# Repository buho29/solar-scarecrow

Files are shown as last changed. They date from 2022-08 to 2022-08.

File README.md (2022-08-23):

# Espantapájaros Solar

Para desanimar a los pájaros a usar nuestra huerta como un restaurante buffet-free
mi segundo intento de ahuyentar de forma not-letal (mi coche muchas veces vive en la calle)

### Descripción 

- "imita" el aleteo de un pájaro
- emite sonidos (mp3)
- solar (queda probar en dias nublados , en autonomia deberia dar para 4 dias sin luz)
- tiene un timón para que el búho gire según la dirección de el viento
- queda probar si es waterproof , uso una junta de un filamento de tpu de 1.75mm pegada con cyano, la electronica descansa sobre una esponja

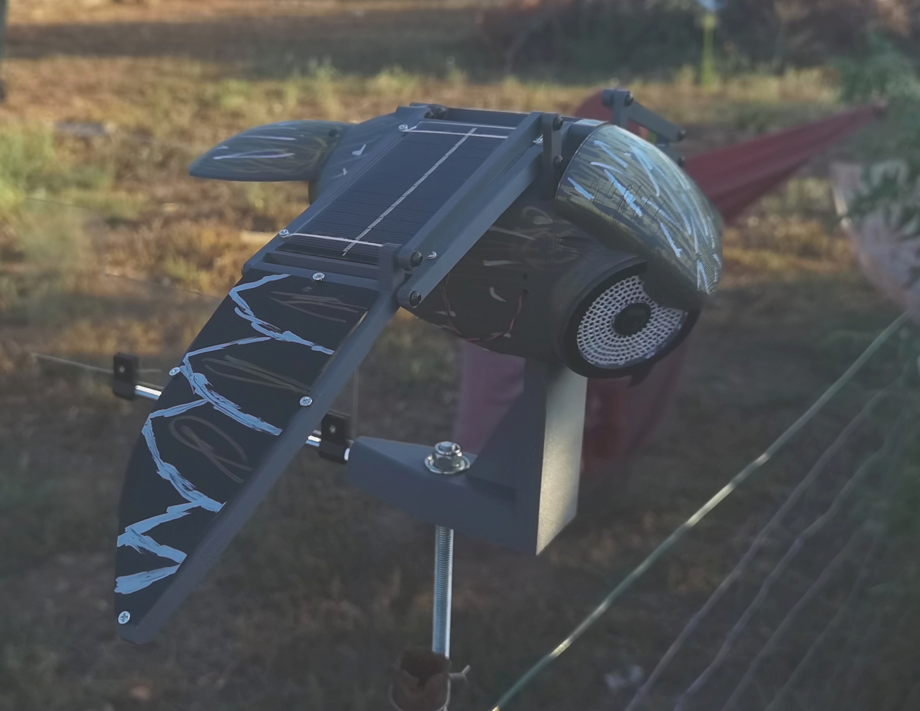
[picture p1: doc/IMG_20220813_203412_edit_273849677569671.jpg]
final


https://user-images.githubusercontent.com/47985666/186021702-38a5164b-d2b8-40fa-a175-db5c7b3ff85f.mp4

*Read this in other languages: [English](README.en.md)

# Ficheros 3D

https://user-images.githubusercontent.com/47985666/186019331-49d15a59-9388-4942-bd01-0e9cbd2d4d04.mp4

los ficheros para imprimir estan en [/stl](/stl).

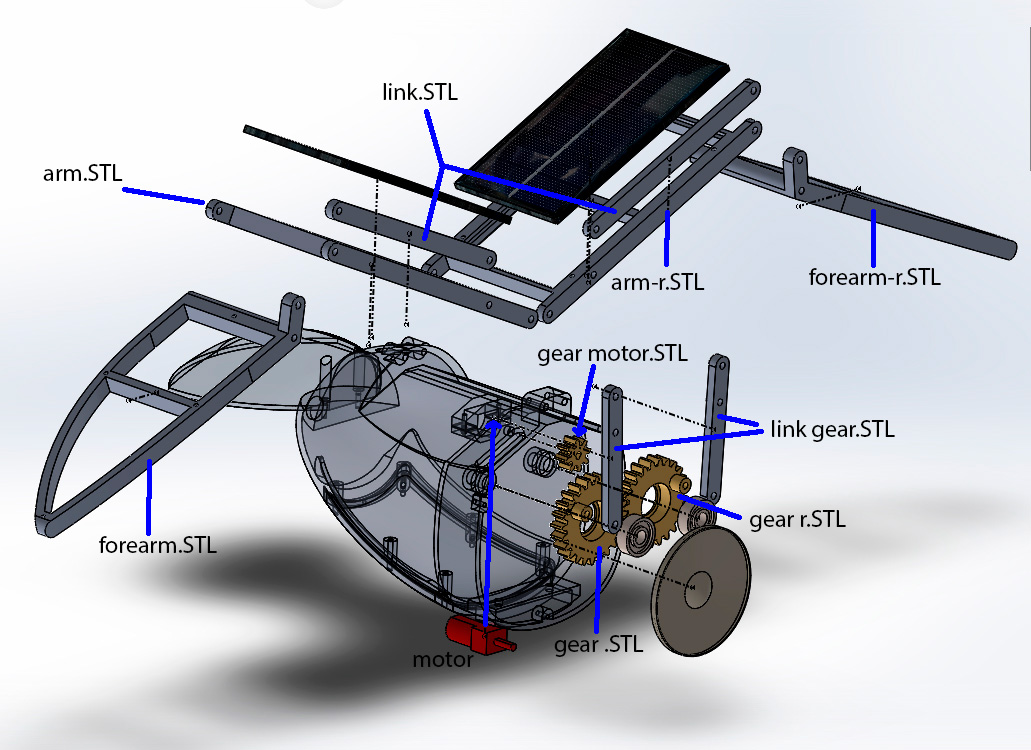
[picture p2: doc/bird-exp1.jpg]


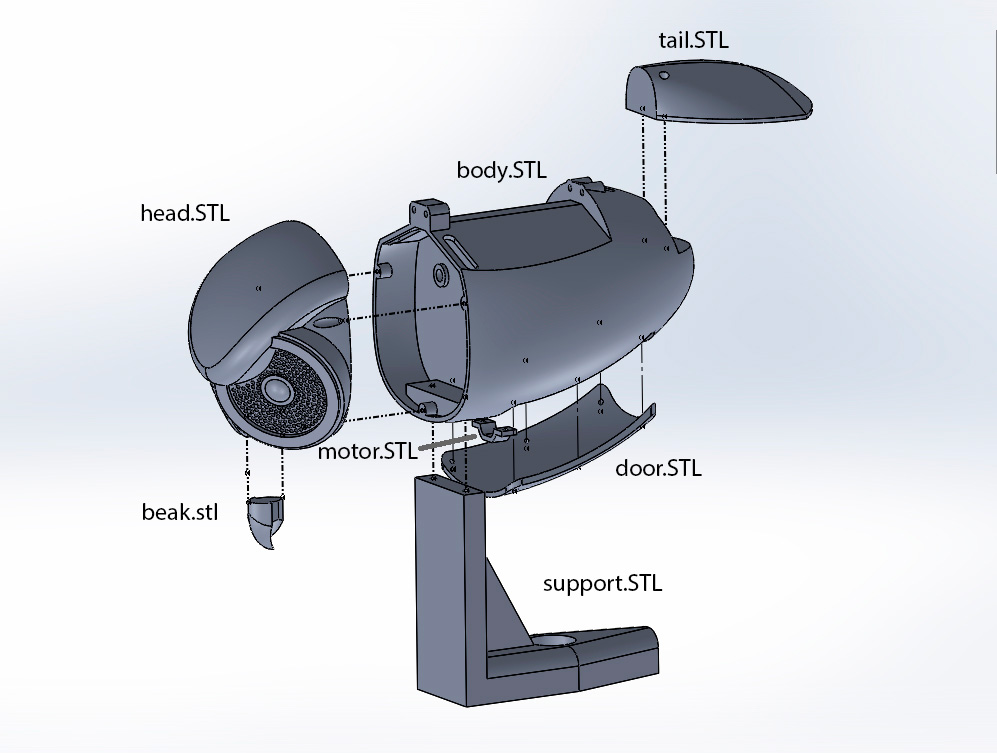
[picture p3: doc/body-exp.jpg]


> **Nota:** los ficheros fuentes de Solidworks 2018 3D estan [/solidworks](/solidworks).

# Hardware

Posiblemente no sea la mejor selección de los materiales pero es la que tenia...

## Suministro electrico

Uso un stepup para alimentar el esp32 y los motores con 6v, el stepup sube el voltaje 4.2v de las baterias a 6v

con el esp32 en modo sleep (ahoro) el consumo real es de 18ma (*24h)

Las 2 placas solares en paralelo bajo el sol me da unos 120ma/h 

Cargo las baterias con un tp4056 , 
necesitas baterías con protección de bajo voltaje , los bms habría sido mejor una mejor elección

Mido la corriente de las placas solares con una divisor de tension (7.2v -> 3.3v)

## Circuito 

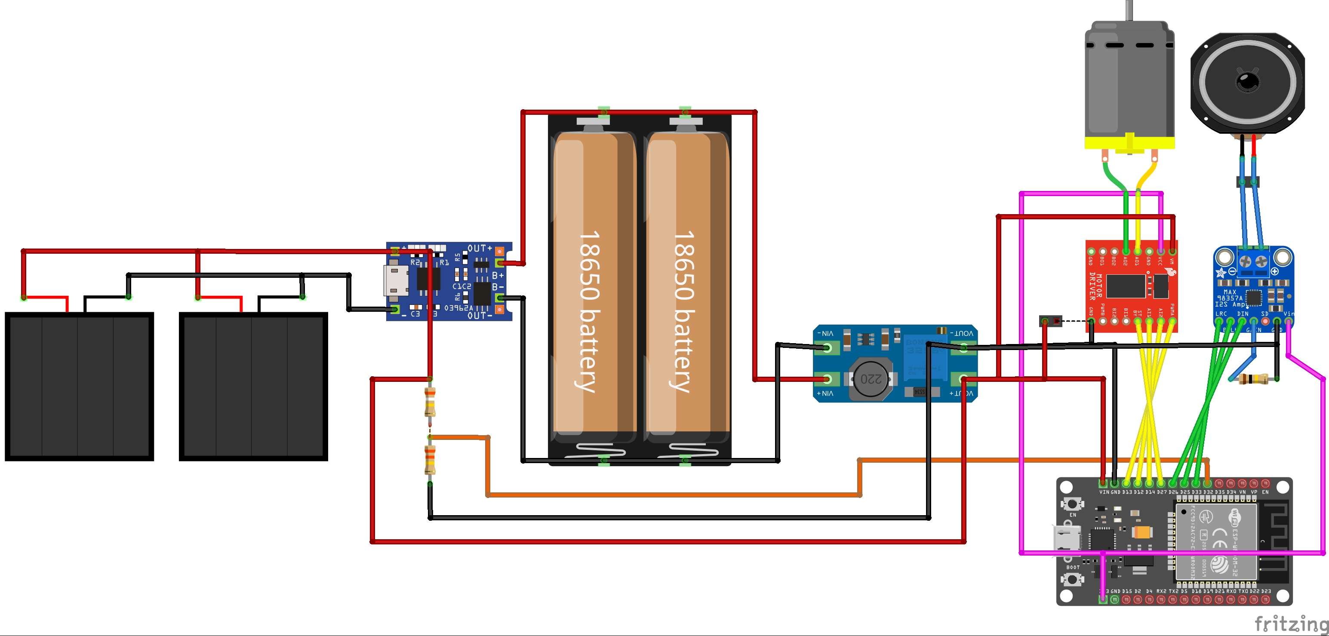
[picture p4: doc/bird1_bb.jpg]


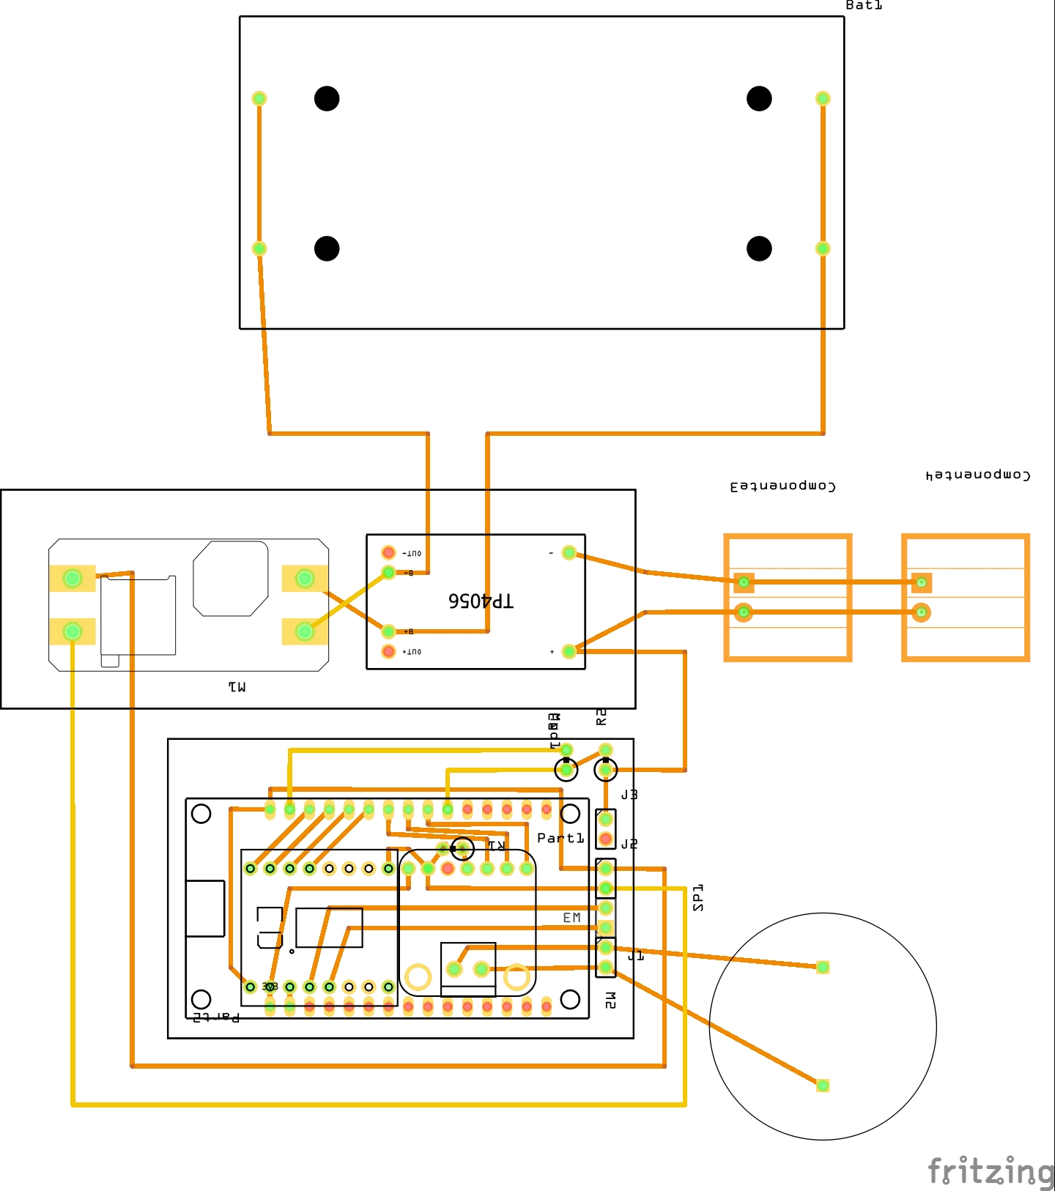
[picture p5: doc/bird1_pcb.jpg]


> **Nota:** los ficheros fuentes de fritzing estan [/electro](/electro).

## Arduino

- Hay que subir el directorio /Data al Spiff del esp32, contiene los *.mp3, se puede poner lo que quieras hasta 1.5mb (reggaton???)
https://github.com/me-no-dev/arduino-esp32fs-plugin

- Hay que instalar esta librería para el max
https://github.com/earlephilhower/ESP8266Audio

### Funcionamiento

```mermaid
flowchart  TD  
 A[Inicio]  -->  B{Es de dia?}  
 B  -- No --> C[Duerme 10min]  
 B  -- Si --> E{El contador es <br> un numero Par?}
 E -- Si --> F[10seg audio+motor]
 E -- No --> G[10seg solo motor]
 F --> C
 G --> C
 C --> B
```
### Variables

```c++
// config
// cuando acabe lo mandamos al modo sleep (ahoro de bateria) 10min 
const int timeSleep = 60 * 10  * uS_TO_S_FACTOR;
// el tiempo que funciona audio y el motor (10seg) 
const int timeRunning = 10 * 1000; 
// el volumen de el audio (maximo 3.99)
const float volume = 1.5;
//si el voltage es menor lo mandamos al sleep (se supone que es de noche)
const float minVoltage = 0.5; 
int _speed = 255; // velocidad del motor (0-255)

```

## Lista de la compra

> **Nota:** no tengo nada que ver con los vendedores, son los enlaces de mi compra.

1 x DC 6V N20 Mini Micro Metal Gear Motor with Gearwheel DC Motors 30 RPM
https://www.aliexpress.com/item/33022320164.html

1 x Dual Motor Driver 1A TB6612FNG
https://www.aliexpress.com/item/32223093678.html

3 x 3PIN and 1 x 2Pin PCB Screw Terminals Blocks Connector 2.54MM Pitch 
https://www.aliexpress.com/item/1005001711075410.html

2 x Mini 6V 1W Solar Panel 
https://www.aliexpress.com/item/32817603341.html

1 x Single Cell Micro USB Power Supply Board TP4056
https://www.aliexpress.com/item/32964995078.html

1 x MT3608 DC-DC Step Up Power
https://www.aliexpress.com/item/32671989238.html

1 x speaker waterproof 8 ohm 3W Diameter 57MM
https://www.aliexpress.com/item/1005002657272394.html

1 x 18650 Battery box double holder
https://www.aliexpress.com/item/4000098297232.html

1 x Max98357 I2S 3W Class D Amplifier
https://www.aliexpress.com/item/4000086613283.html

1 x Esp32 DEVKIT V1
https://a.aliexpress.com/_vYtC43

2x Battery 18650 with protection

### Otros

#### Rodamientos
2x 606ZZ 6x17x6mm (gears)
https://www.aliexpress.com/item/1005001826957482.html

2 x 608ZZ 8x22x7mm (rudder)
https://www.aliexpress.com/item/4001058241232.html

#### Tornilleria
wooden Self-tapping screw M2x8mm and M2x6mm
https://www.aliexpress.com/item/1005002336941795.html

18 x Screw M3 x 12mm
https://www.banggood.com/M3-Bolts-Stainless-Steel-Screws-Button-Head-Socket-Cap-10-Size-p-952124.html

### Herramientas
#### Brocas :
- 3mm(better 3.1) 
- 2.8mm (thread) 
- 2mm
- 1.6mm (thread)

## Galeria

gallery
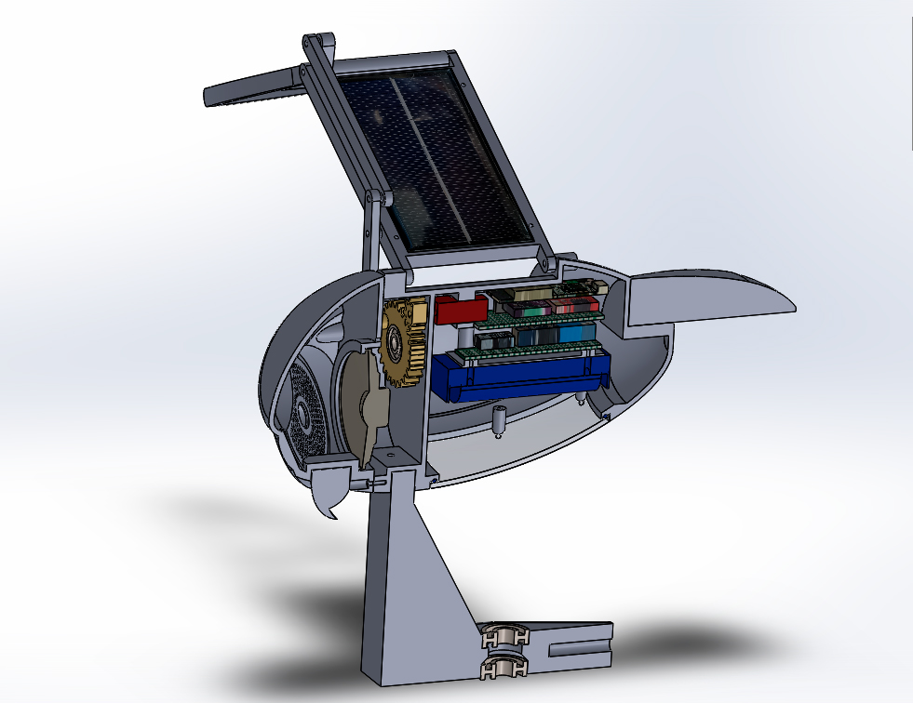
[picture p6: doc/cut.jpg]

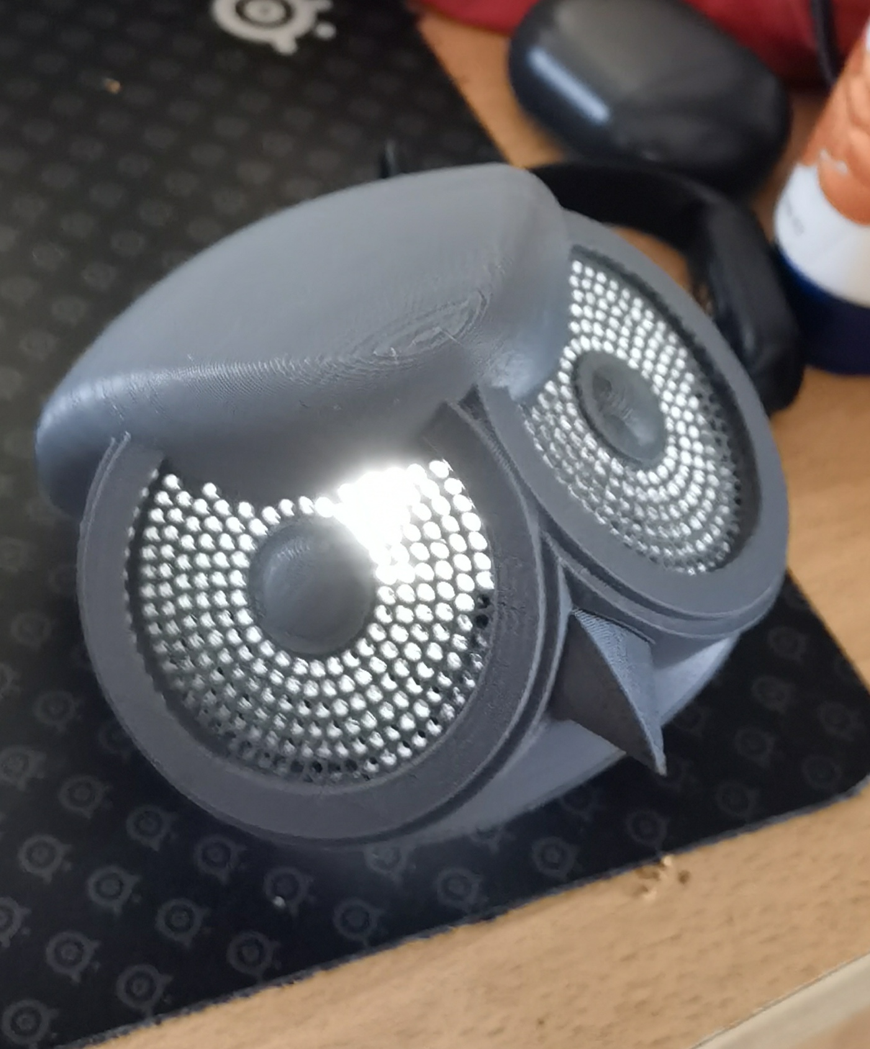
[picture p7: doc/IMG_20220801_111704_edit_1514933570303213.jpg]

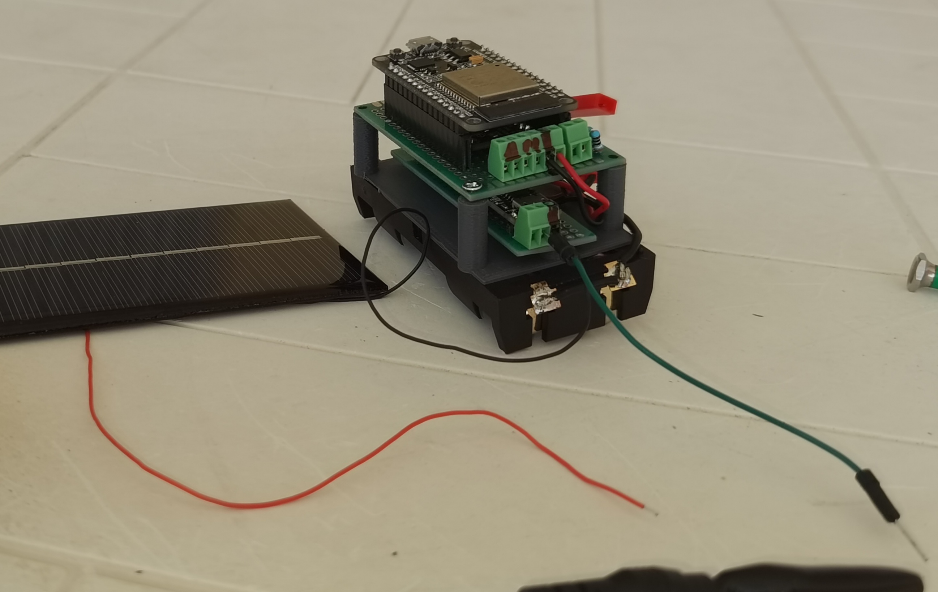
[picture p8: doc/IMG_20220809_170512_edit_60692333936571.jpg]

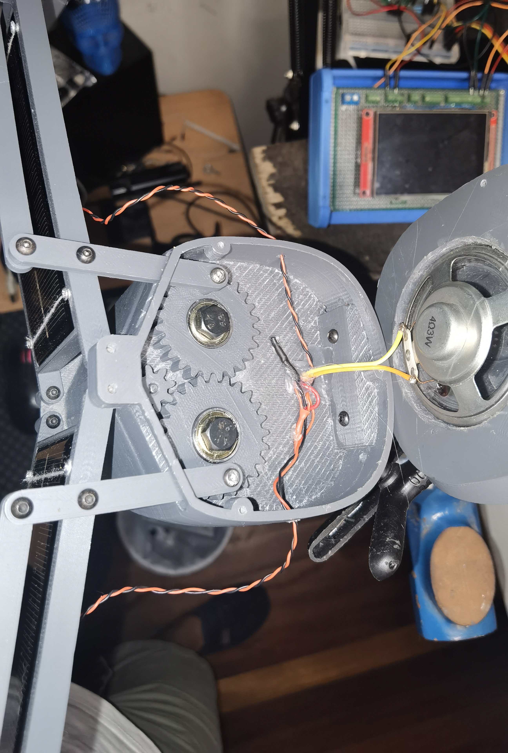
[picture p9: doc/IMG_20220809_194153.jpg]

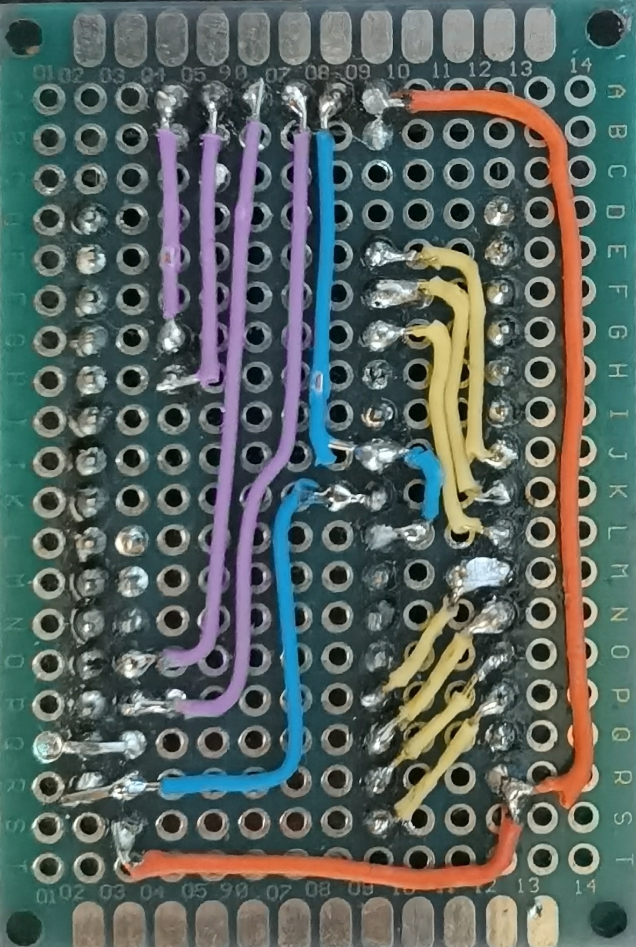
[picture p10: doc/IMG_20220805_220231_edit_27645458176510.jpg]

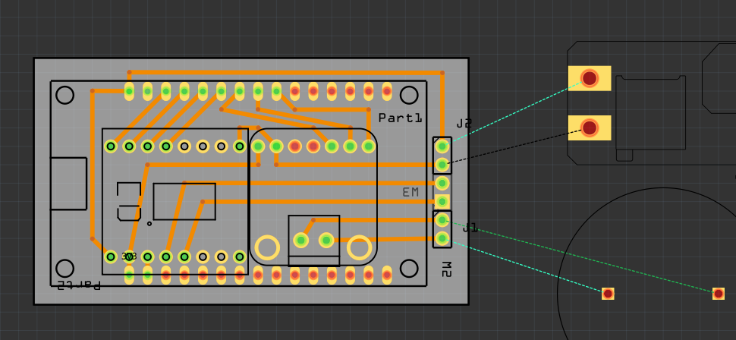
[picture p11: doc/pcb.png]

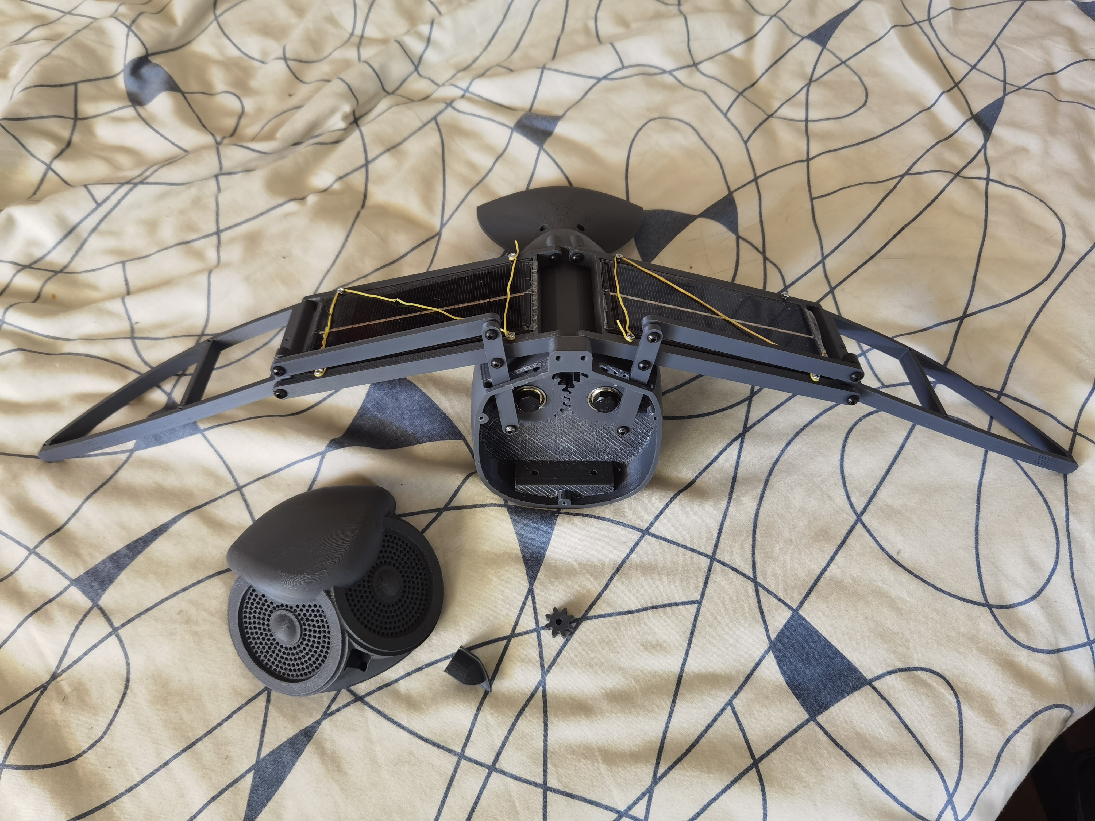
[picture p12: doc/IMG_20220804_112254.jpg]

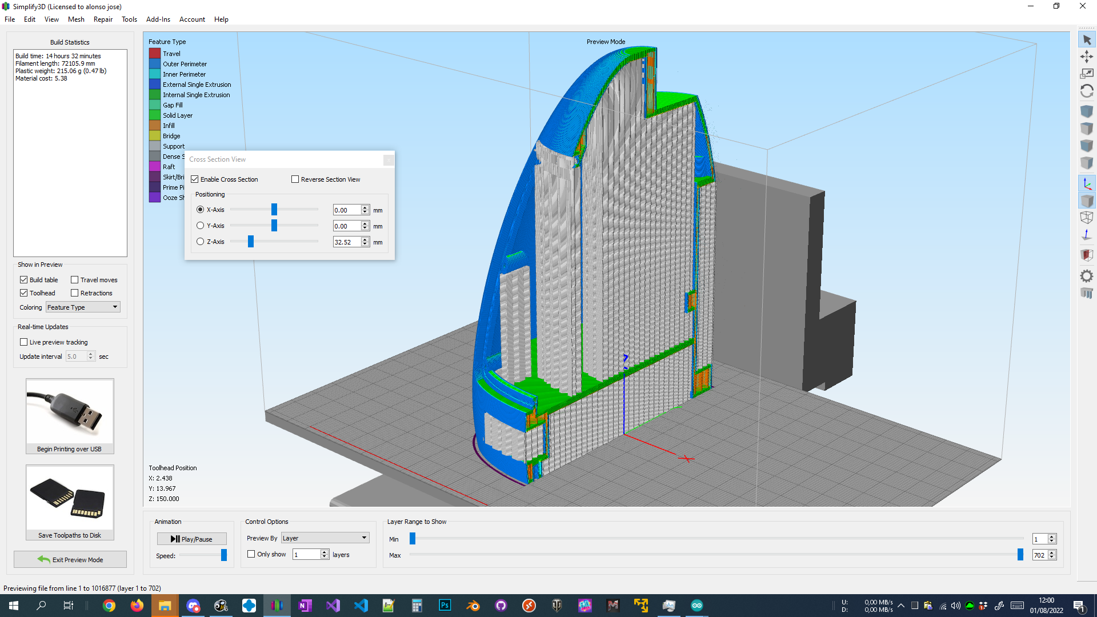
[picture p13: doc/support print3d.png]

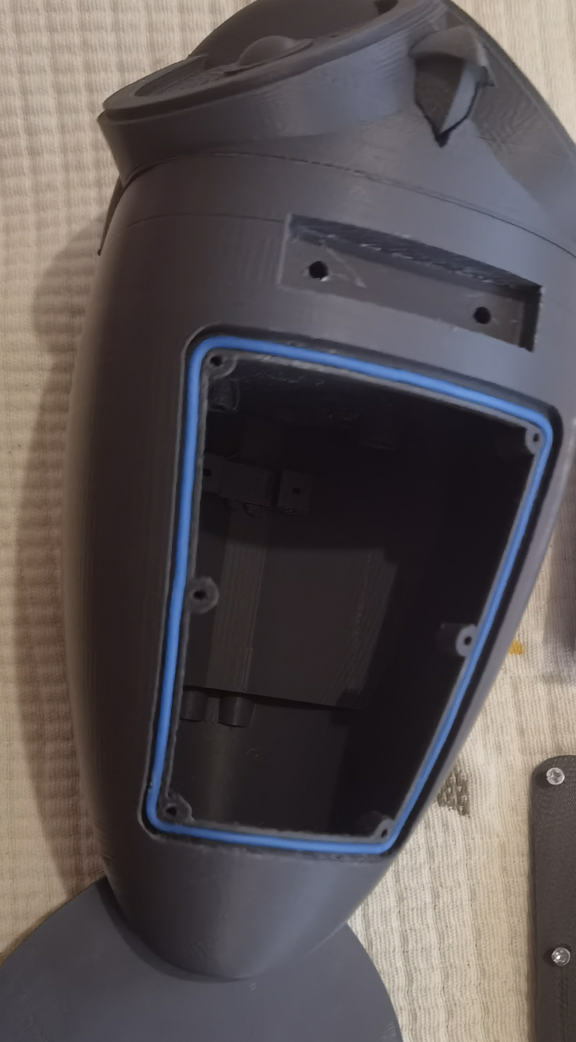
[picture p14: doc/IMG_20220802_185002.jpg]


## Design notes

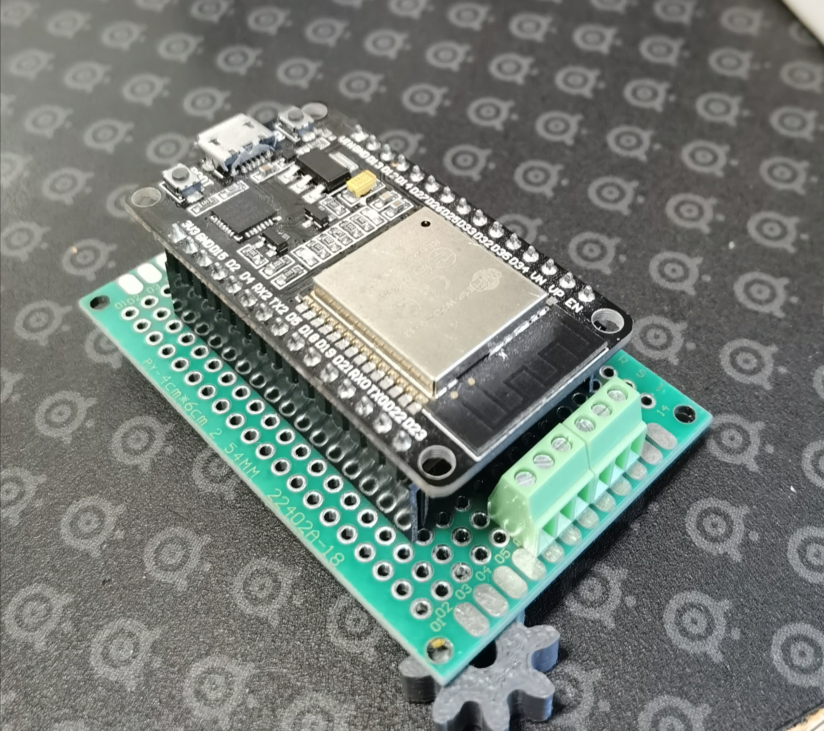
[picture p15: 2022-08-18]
doc/IMG_20220805_130451_edit_7011887212471.jpg

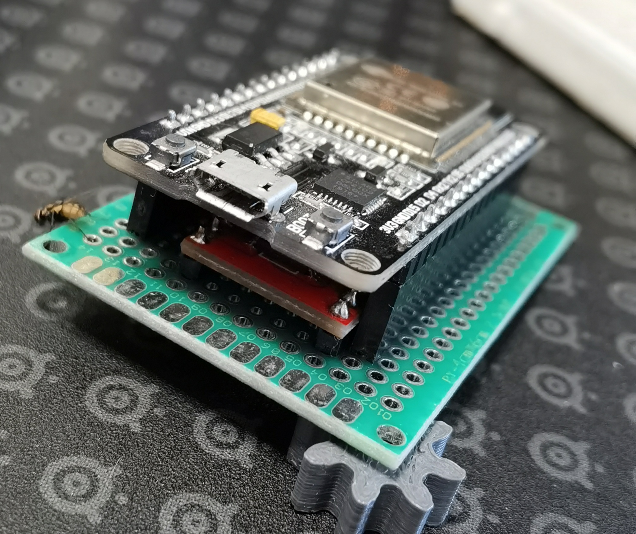
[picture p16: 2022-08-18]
doc/IMG_20220805_130421_edit_7032362407259.jpg

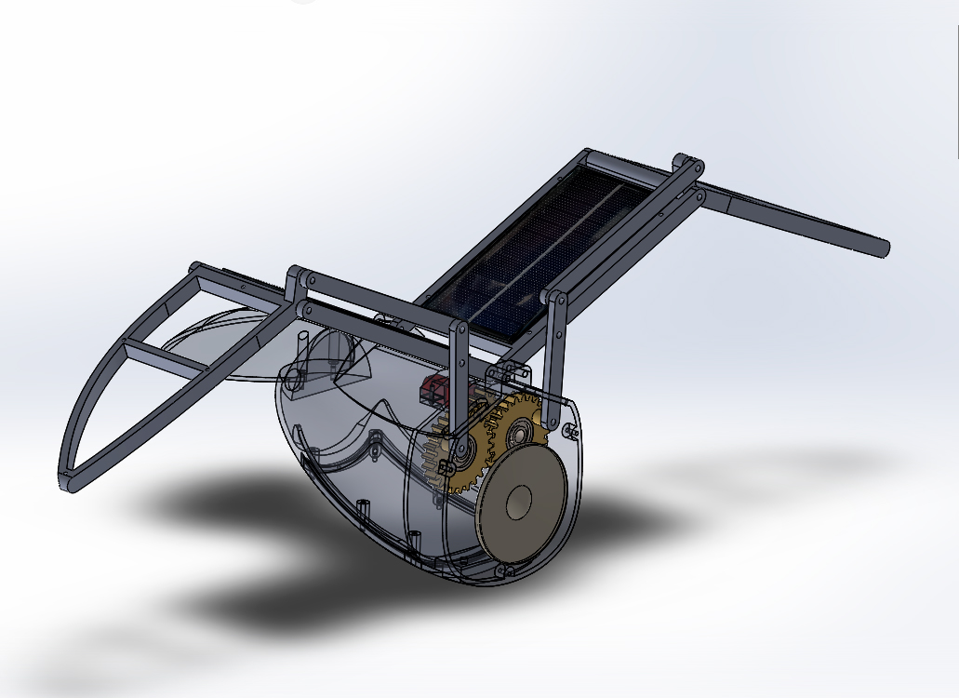
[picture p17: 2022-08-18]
doc/bird-exp.jpg

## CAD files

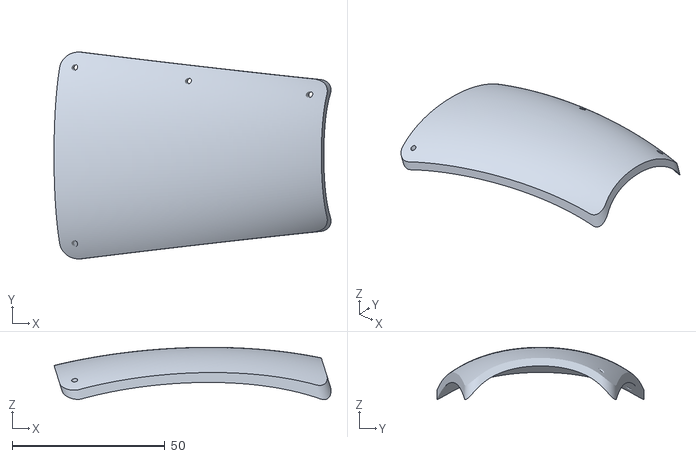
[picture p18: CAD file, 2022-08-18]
stl/door.STL
90.8 x 67.8 x 17.2

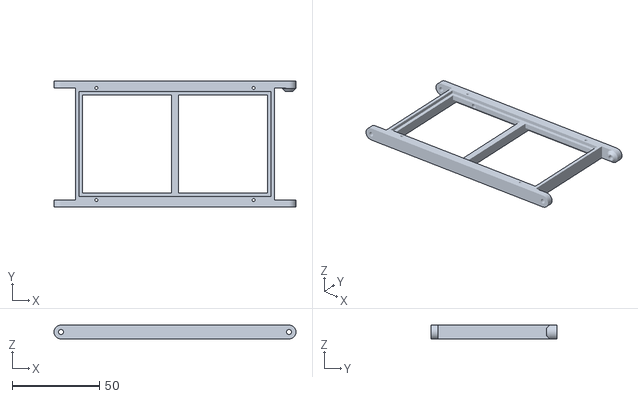
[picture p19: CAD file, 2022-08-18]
stl/arm.STL
139.0 x 72.4 x 8.00

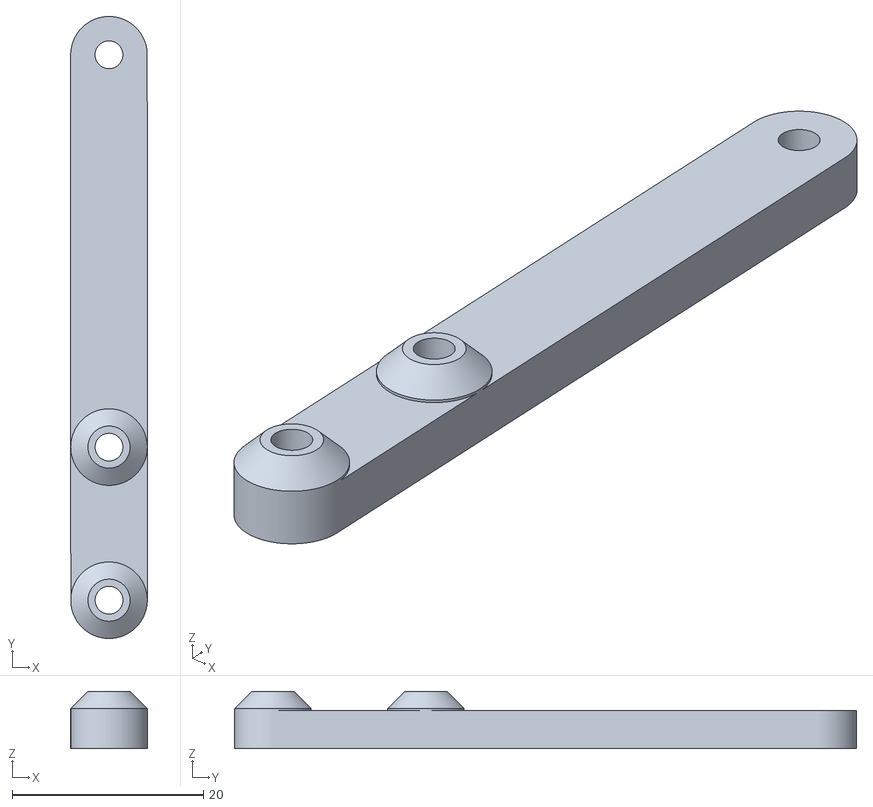
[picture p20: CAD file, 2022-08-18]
stl/link gear.STL
8.01 x 65.0 x 6.00

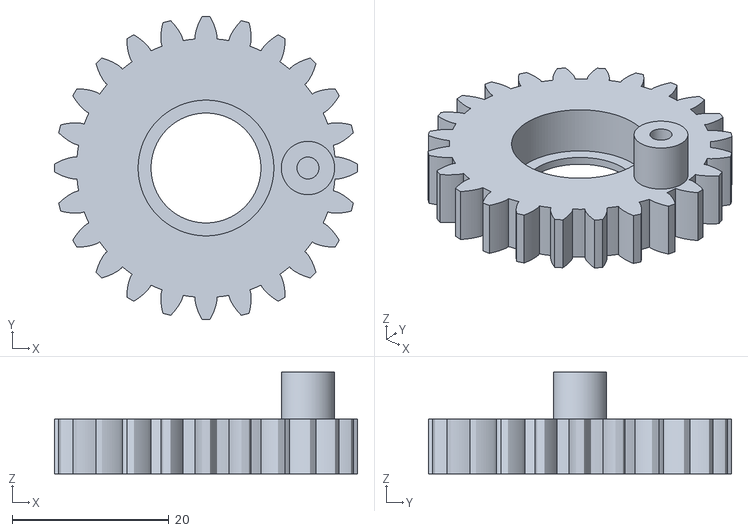
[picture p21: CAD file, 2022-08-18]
stl/gear .STL
38.6 x 38.6 x 13.0

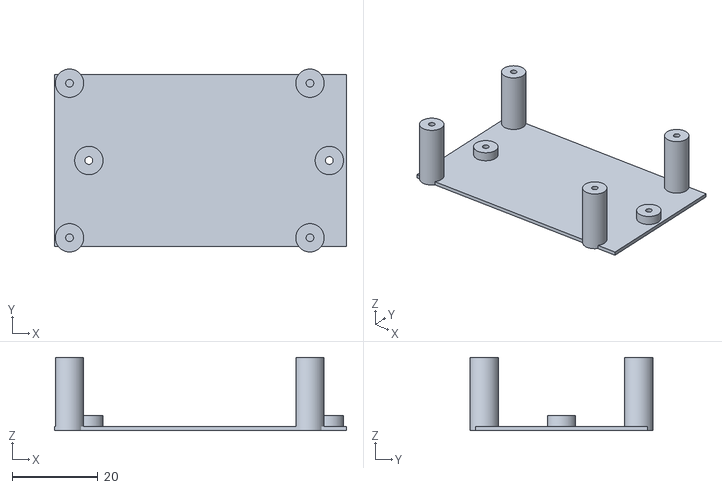
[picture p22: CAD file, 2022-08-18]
stl/support elect.STL
68.0 x 42.6 x 17.1

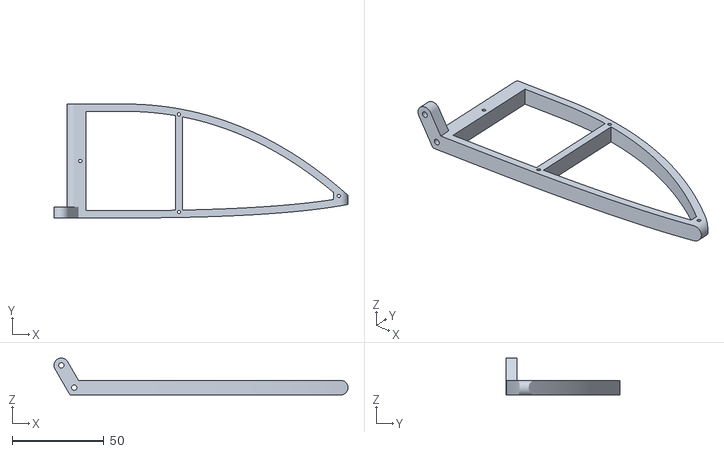
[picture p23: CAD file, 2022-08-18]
stl/forearm-r.STL
160.0 x 62.0 x 20.1

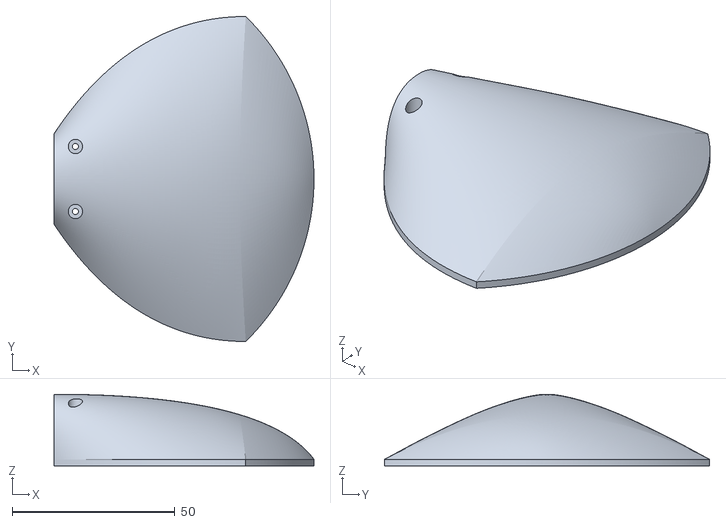
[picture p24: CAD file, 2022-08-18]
stl/tail.STL
80.0 x 100.0 x 22.0

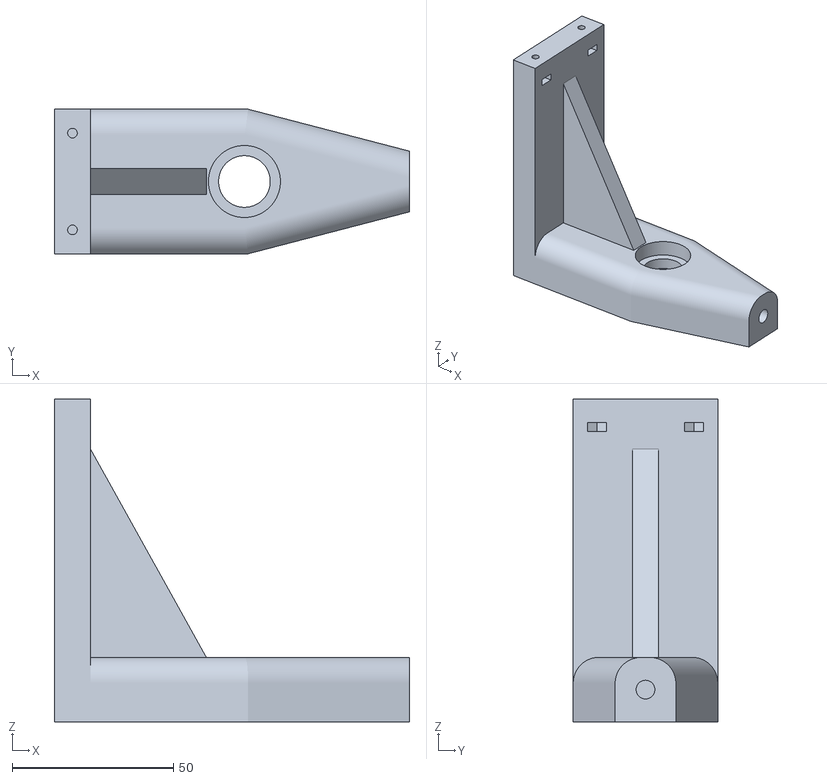
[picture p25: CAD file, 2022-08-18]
stl/support.STL
110.0 x 44.8 x 100.0

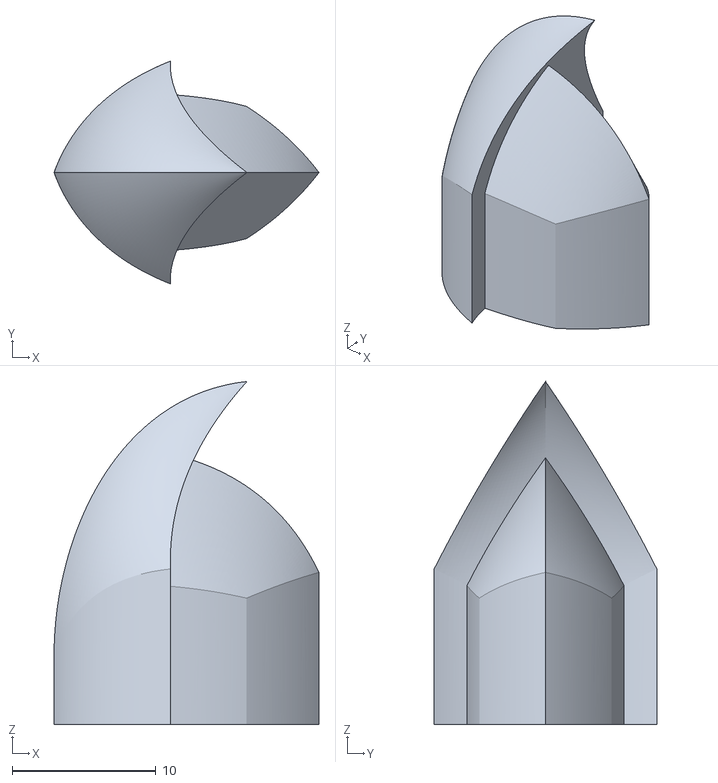
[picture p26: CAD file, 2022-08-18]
stl/beak.stl
18.5 x 15.5 x 23.9

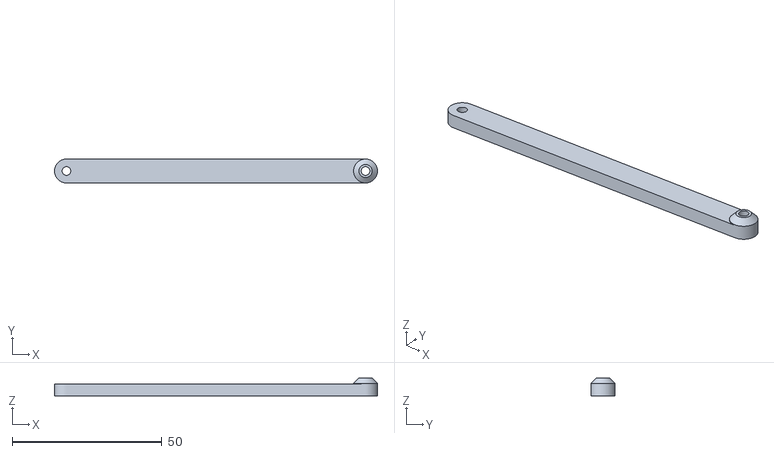
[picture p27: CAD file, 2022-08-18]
stl/link.STL
108.0 x 8.00 x 6.00

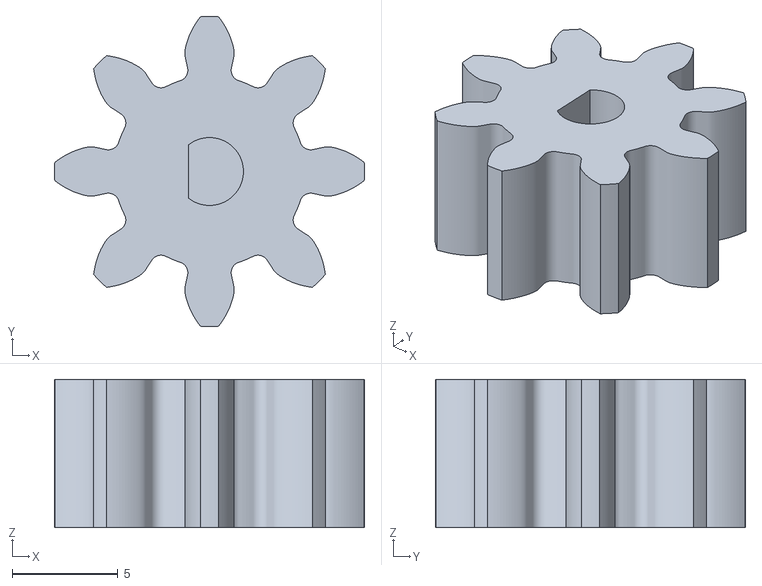
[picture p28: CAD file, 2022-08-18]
stl/gear motor.STL
14.6 x 14.6 x 7.00

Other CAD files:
stl/arm-r.STL
stl/forearm.STL
stl/gear r.STL

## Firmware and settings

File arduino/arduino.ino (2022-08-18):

#include <Arduino.h>
#include <SPIFFS.h>
//https://github.com/earlephilhower/ESP8266Audio
#include <AudioFileSourceSPIFFS.h>
#include <AudioGeneratorMP3.h>
#include <AudioOutputI2S.h>


#define uS_TO_S_FACTOR 1000000ULL  /* Conversion factor for micro seconds to seconds */

// config
const int timeSleep = 60 * 10  * uS_TO_S_FACTOR;
const int timeLongSleep = 60 * 15 * uS_TO_S_FACTOR;
const int timeRunning = 10 * 1000;
const float volume = 1.5;//0.026;//3.99;//
const float minVoltage = 0.5; //go long sleep
int _speed = 255; // speed motor
 
// pin audio

const int pinBCK = 25;
const int pinLRCK = 33;
const int pinDATA = 26;

// pin motor
const int pinPWMA = 13;
const int pinAIN2 = 12;
const int pinAIN1 = 14;
const int pinSTBY = 27;

// solar reading pin voltage 7.2v
const int pinINPUT = 32;

// variables
enum direction {
   clockwise,
   counterClockwise
};

RTC_DATA_ATTR int indexList = 0;
RTC_DATA_ATTR unsigned int countRun = 0;
bool isPlaying= false;
int countList = 0;
char playList[20][40];

AudioGeneratorMP3 *mp3;
AudioFileSourceSPIFFS *file;
AudioOutputI2S *out;

const int pinMotorA[3] = { pinPWMA, pinAIN2, pinAIN1 };
direction dir;

float fmap(float x, float in_min, float in_max, float out_min, float out_max)
{
  return (x - in_min) * (out_max - out_min) / (in_max - in_min) + out_min;
}

void enableMotors(bool value)
{ 
  if(value) digitalWrite(pinSTBY, HIGH);
  else digitalWrite(pinSTBY, LOW);
}

void setupMotor()
{
   pinMode(pinPWMA, OUTPUT);
   pinMode(pinAIN2, OUTPUT);
   pinMode(pinAIN1, OUTPUT);
   pinMode(pinSTBY, OUTPUT);
   
   enableMotors(true);
}

void moveMotor(int dir,const int pinMotor[3], int speed)
{
  if(dir == clockwise){
    digitalWrite(pinMotor[1], LOW);
    digitalWrite(pinMotor[2], HIGH);
    analogWrite(pinMotor[0], speed);    
  }else{
    digitalWrite(pinMotor[1], HIGH);
    digitalWrite(pinMotor[2], LOW);
    analogWrite(pinMotor[0], speed);    
  }
}

void scanSound()
{
    File root = SPIFFS.open("/");
    if(!root || !root.isDirectory()) return;

    File file = root.openNextFile();
    while(file){
        if(!file.isDirectory()){
            //Serial.println(file.name());

            strcpy(playList[countList], "/");
            strcat(playList[countList], file.name());
            countList++;
        }
        file = root.openNextFile();
    }
}

void setupAudio()
{
  SPIFFS.begin();

  scanSound();
  
  out = new AudioOutputI2S();
  out->SetPinout(pinBCK, pinLRCK, pinDATA);
  out->SetGain(volume);
  
  mp3 = new AudioGeneratorMP3();
}

void play(const char* nameFile)
{
  Serial.println(String ("play :")+ nameFile);
  file = new AudioFileSourceSPIFFS(nameFile);
  mp3->begin(file, out);
}

void setup() 
{
  Serial.begin( 115200 ); 

  delay(1000);

  // scale 3.3v 7.2v max 
  float voltage = fmap(analogRead(pinINPUT), 0.0f, 4095.0f, 0.0f, 7.2f);
  Serial.println(voltage);
  
  if(voltage < minVoltage)
  {
    Serial.println("sleep long");
    //sleep long
    esp_sleep_enable_timer_wakeup(timeLongSleep);
    esp_deep_sleep_start();
  }
  //init
  setupMotor();
  moveMotor(counterClockwise,pinMotorA, _speed);

  Serial.println("motor");
  // 
  if(countRun % 2 == 0)
  {
    isPlaying = true;
    Serial.println("audio");
    setupAudio();
    play(playList[indexList]); 
  }

  countRun++;
}

void loop ()
{  
  //float voltage = fmap(analogRead(pinINPUT), 0.0f, 4095.0f, 0.0f, 7.2f);
  //Serial.println(voltage);

  //sleep
  if (millis() > timeRunning) 
  {
    // stop all
    if(isPlaying && mp3->isRunning()) mp3->stop();
    enableMotors(false);
    
    if (isPlaying){
      // next sound index
      indexList++;
      if(indexList>=countList) indexList = 0; 
    }
    Serial.println("sleep");
    esp_sleep_enable_timer_wakeup(timeSleep);
    esp_deep_sleep_start();
  }
  // mp3->loop();
  if (isPlaying && mp3->isRunning() && !mp3->loop()) mp3->stop();
  //repeat sound (loop)
  else if (isPlaying && !mp3->isRunning()) play(playList[indexList]);
}

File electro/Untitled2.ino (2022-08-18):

// i2s pins
i2s_pin_config_t i2sPins = {
    .bck_io_num = 25,//this is BCK pin
    .ws_io_num = 33,// this is LRCK pin
    .data_out_num = 26,// this is DATA output pin
    .data_in_num = -1
};



const int pinPWMA = 13;
const int pinAIN2 = 12;
const int pinAIN1 = 14;
const int pinSTBY = 27;


// motor

enum direction {
   clockwise,
   counterClockwise
};


int speed = 255;//velocidad de giro
direction dir;

const int pinMotorA[3] = { pinPWMA, pinAIN2, pinAIN1 };

void enableMotors()
{
   digitalWrite(pinSTBY, HIGH);
}

void disableMotors()
{
   digitalWrite(pinSTBY, LOW);
}

void setupMotor()
{
   pinMode(pinPWMA, OUTPUT);
   pinMode(pinAIN2, OUTPUT);
   pinMode(pinAIN1, OUTPUT);
   pinMode(pinSTBY, OUTPUT);
   
   enableMotors();
}

//Funciones que controlan los motores
void moveMotorForward(const int pinMotor[3], int speed)
{
   digitalWrite(pinMotor[1], HIGH);
   digitalWrite(pinMotor[2], LOW);

   analogWrite(pinMotor[0], speed);
}

void moveMotorBackward(const int pinMotor[3], int speed)
{
   digitalWrite(pinMotor[1], LOW);
   digitalWrite(pinMotor[2], HIGH);

   analogWrite(pinMotor[0], speed);
}


void turn(int d)
{
   if (d == clockwise) moveMotorBackward(pinMotorA, speed);
   else moveMotorForward(pinMotorA, speed);
}
.

void setup() {
  Serial.begin( 115200 ); 
  setupMotor();
  //
  moveMotorForward(pinMotorA, 255);
  //delay(5000);
}

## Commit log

2022-08-18 Create bateria x2 18650.SLDPRT
    [bateria x2 18650.SLDPRT]
2022-08-18 Create bird solar.SLDASM
    [bird solar.SLDASM]
2022-08-18 Create link gear.SLDBLK
2022-08-18 Create charger 1 cell.SLDPRT
    [charger 1 cell.SLDPRT]
2022-08-18 Create DOIT Esp32 DevKit v1 improved.fzpz
2022-08-22 up1
    up1
    [6612.SLDPRT, Ensamblaje3.SLDASM, aguja.SLDPRT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]
